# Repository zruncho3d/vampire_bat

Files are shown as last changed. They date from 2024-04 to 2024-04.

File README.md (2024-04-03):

## Vampire Bat - a pinned extrusionless gantry with pin-in-tube belt clips
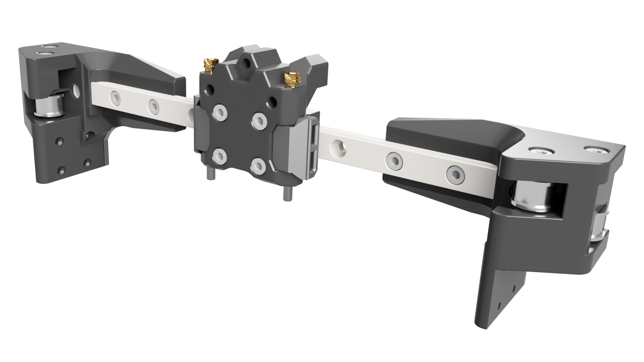
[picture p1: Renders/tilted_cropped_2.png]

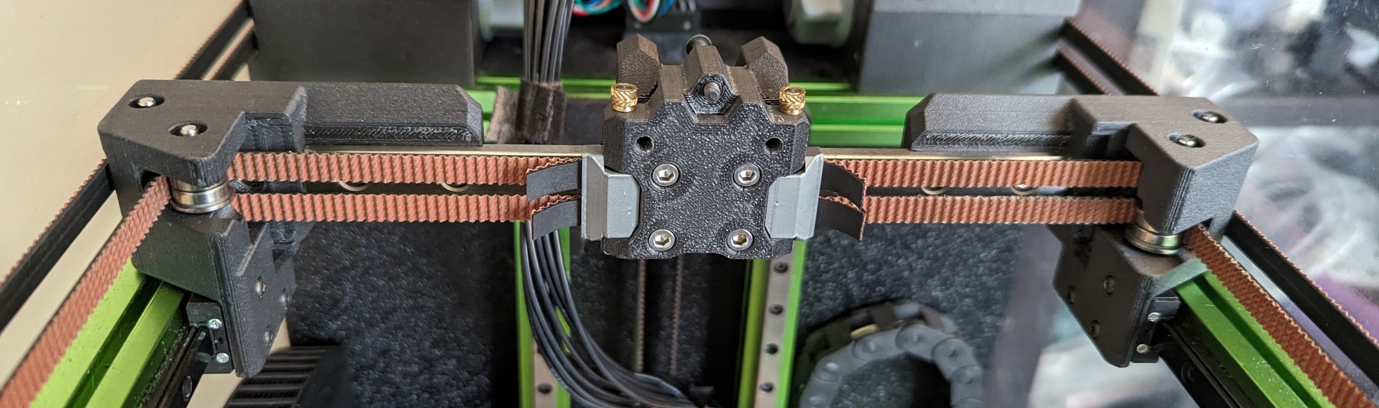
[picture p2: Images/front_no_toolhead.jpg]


The **Vampire Bat** gantry system includes 3 distinct parts:

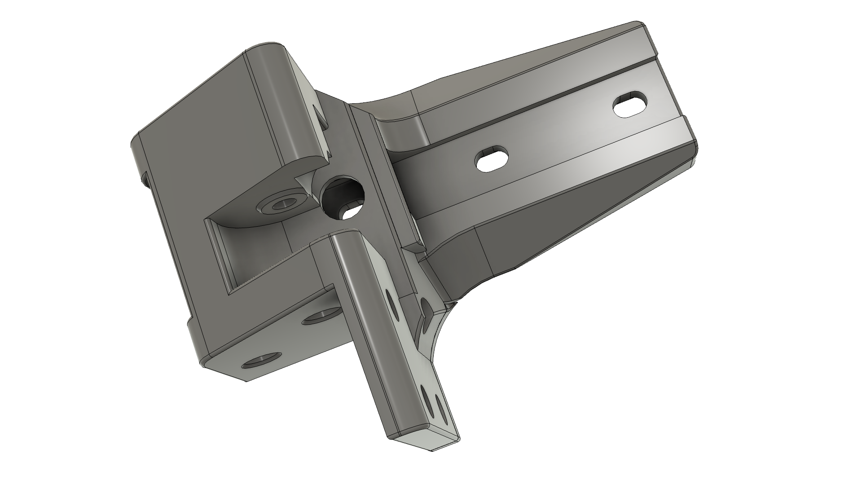
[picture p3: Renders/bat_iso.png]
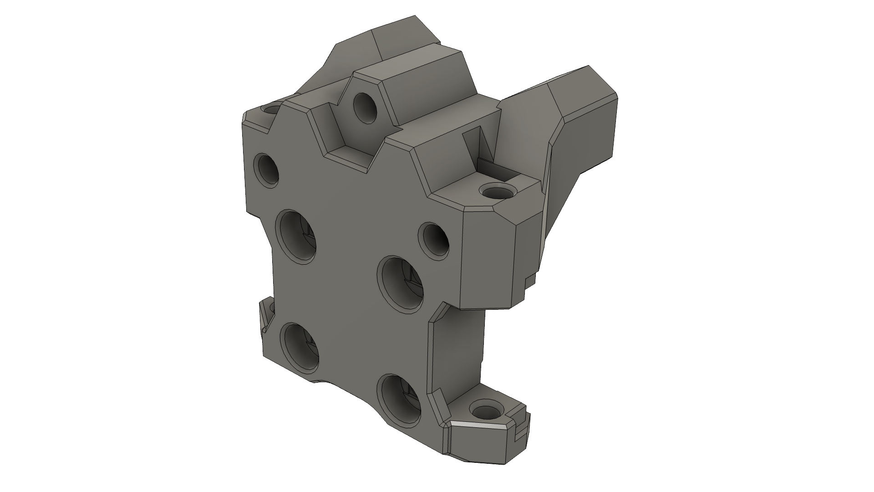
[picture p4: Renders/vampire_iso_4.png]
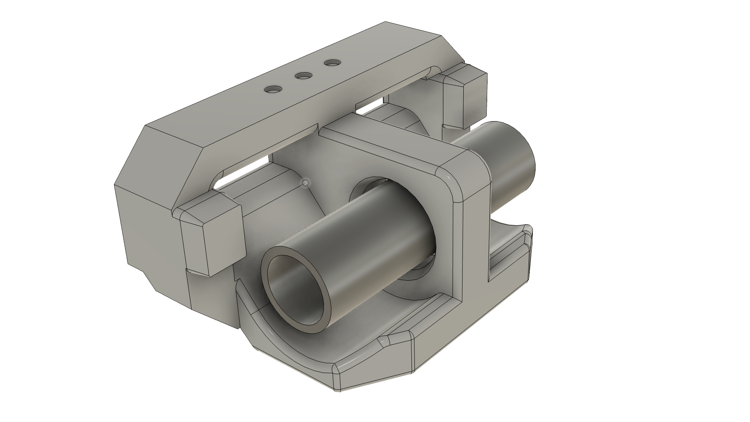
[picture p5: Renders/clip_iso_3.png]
|  |  |  |
| --- | --- | --- |
| **Bat** XY joints | **Vampire** pinned X carriage | **Vampire** pin-in-tube belt clips |

**Together**: these 3 parts yield a rigid, easier-to-build, easier-to-install-belts gantry that drops into an otherwise-stock V0, with little-to-no X or Y travel loss!

**Bat XY joints only**: *Not ready to enter the world of pins, clips, and tubes?  No problem.*    Pick your favorite front-facing X carriage from many choices - Micron, Salad Fork, Pandora/Pandora's Box, Boop, and mmaybe even Archetype and Xol carriages in the future.  Few toolheads fit a V0.2 mount, so more options for interesting new toolheads on smaller printers is a Good Thing.

**Vampire X carriage and clips only**: *Don't have a V0?  No problem.*  Enable the ease of pins on any Micron, Salad Fork, Dueling Zero, or Pandora's Box: faster attachment and completely repeatable tensioning. You can then swap out motors, or swap out rails, in just minutes, without needing to retighten and rematch belt tensions. Should work on any PFA printer with 6mm belts, 3mm belt spacing, and a front-facing MGN9H rail.  

## Updates

* 2024-04-03: Thanks `thor`!  Fixed minor bridging issues near MGN9 entrance and belt tunnel.
* 2024-04-02: Added IS Graphs.

## Features
* Compatibility with MiniSB and derivatives (Mini Stealth Sherpa, Hacky Boi, and more)
* Compatibility with most front-facing PFA carriages, including Boop
* Faster assembly from elimination of both washers and spacers ( :tada: )
* Faster belt installation from more-constrained belt paths; no more poking with an allen key from the side, or needing to remove side panels
* Repeatable belt tensioning; can even remove clips while tensioned
* Supports fully pinned bearings, which prevent over-torqueing that can lead to skipped steps and messy resonance graphs
* All screws are easily accessible when mounted
* Full 120mm+ X and Y travel with BoxZero; ~118mm with regular V0

## Support the creator
Like what you see?  [Buy me a coffee](https://ko-fi.com/zruncho3d) to show the love and enable future mods and content - stuff like [F0](https://github.com/zruncho3d/f-zero), [T0](https://github.com/zruncho3d/tri-zero), [B0](https://github.com/zruncho3d/boxzero), [X0](https://github.com/zruncho3d/double-dragon), [D0](https://github.com/zruncho3d/DuelingZero), [DX](https://github.com/zruncho3d/DuelingX), [ZeroPanels](https://github.com/zruncho3d/ZeroPanels), [ZeroClick](https://github.com/zruncho3d/zeroclick), [NoDropNuts](https://github.com/zruncho3d/f-zero/tree/main/STLs/NoDropNuts), [Poke](https://github.com/zruncho3d/poke), and more.

 :heart: *-Zruncho*

Or, read more below if this seems interesting.....

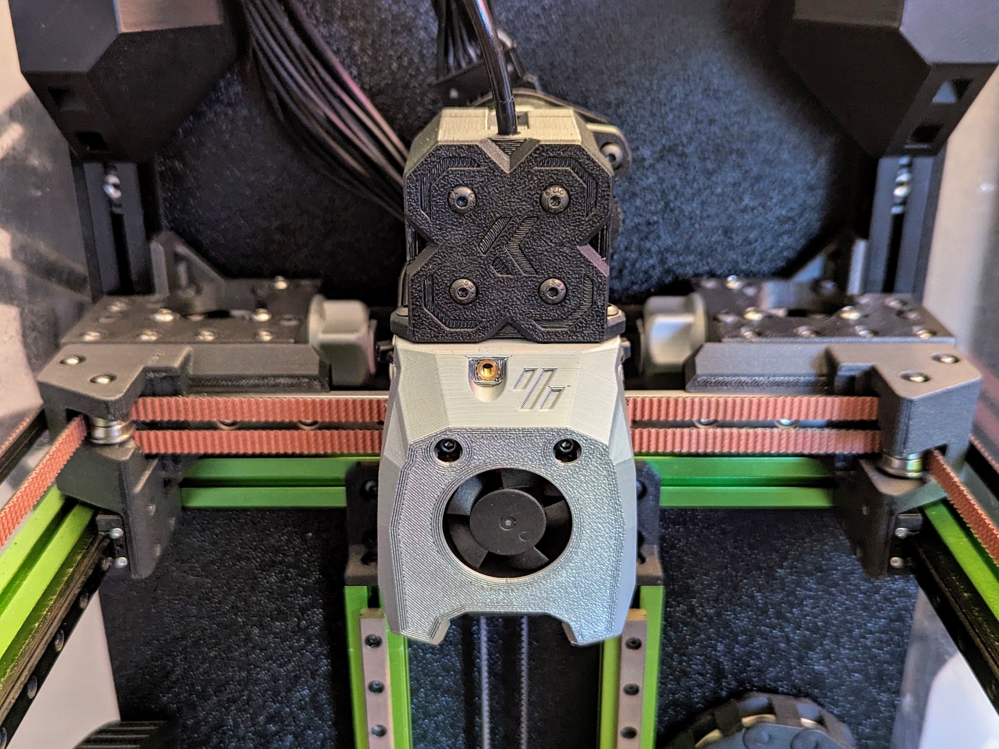
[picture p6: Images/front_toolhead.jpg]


Shown above: gantry parts in 3DXTech CF-ABS + clips in KVP MSIL ABS.  Printer is a custom [Fully-Boxed](https://github.com/zruncho3d/boxzero) [Tri-Zero](https://github.com/zruncho3d/tri-zero) with toolhead by Kevinakasam, plus [Papilio Lite](https://github.com/kevinakasam/Papilio-Belt-Extruder) belt extruder.  This extruder printed the CF-ABS parts like a champ.

## Parts Explained

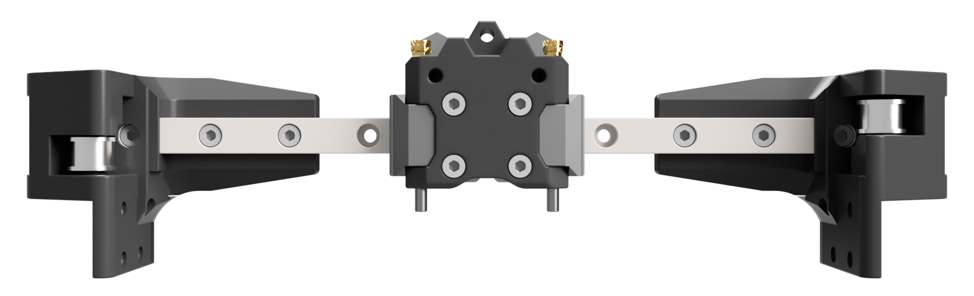
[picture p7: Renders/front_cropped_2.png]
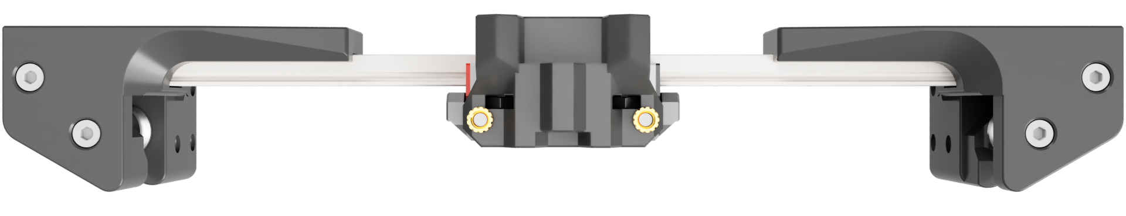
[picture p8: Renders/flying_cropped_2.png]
|  |  |
| - | - |

**Bat XY Joints**: the core idea is to print the XY joints on the rear-facing surface as a single piece, and to constrain the the rail inside (vs as a two-part assembly, on a V0).  Compared to a V0, this is faster and easier to assemble, has way fewer parts (no spacers, washers, or self-tapping screws), is plenty rigid, and is lighter.

The print-orientation concept is based on a [top-facing extrusionless V0 gantry from TheMrFish](
https://discord.com/channels/825469421346226226/875884022285369344/1035022744766652416).  The overall concept is inspired by an [earlier front-facing extrusionless V0 from richardjm](https://github.com/richardjm/voron-parts/tree/main/voron-0.1/Mgn9h).

There's a lot of care to get the tiny vertical bars to acts as supports so that the front-facing filled-in areas can print well.

**Vampire X carriage**: the upper geometry is [Pandora-X-carriage-derived](https://github.com/MasturMynd/Pandora/blob/main/STLs/X_Carriage/MGN9-H_X_Carriage.stl), and includes V0.2-carriage-compatible rear heatset holes for a strain relief or toolhead board.  The CAD derives from [Boop beta-4](https://github.com/PrintersForAnts/Boop/tree/main/beta_4).

**Vampire belt clips**: belts go through a thin slot, then a tube drops in, and the belt wraps around the tube.  The geometry is loosely inspired by [Archetype's clips](https://github.com/Armchair-Heavy-Industries/Archetype/blob/main/Archetype%20Core/Rail%20Mount/%5Ba%5D_belt_clamp_pair.stl), but vastly smaller, and earlier versions were part of [experiments into Pinned Boop](https://www.youtube.com/watch?v=ZaqttrUeE4I).

## Instructions

Required tools:
* (carriage pins option only)
  * small vise
  * ~2.9mm drill bit
* 4mm drill bit for clips
* soldering iron for heatsets

Preferred tools:
* (carriage pins option only) 3mm reamer
* glue

#### Print the parts
* Standard Voron settings are fine.  Add infill beyond 40%, if you'd like; can't hurt.
* This part is near heat; use a temp-resilient material like ABS.

#### Prep the parts
* Remove supports from the XY joints.
* Ream out the two vertical pin holes in the X carriage.  Pins should slide smoothly into the hole.
* Test-fit each tube into a belt clip; may need the 4mm drill bit to open up the hole slightly.
* Test-fit each belt clip into the carriage, and drop the pin in; it should have little to no resistance.  If there's resistance, look through the pin hole and maybe X-acto away a bit of material.
* Screw the 2x M3x30 BHCSes up from the bottom, into the X carriage, until there's a small gap.  Push hard to start forming the threads and make sure they stay aligned against the plastic.
* Assemble pins (2x)
  * Put heatset in a bench vise, with the thin end facing up.
  * Using a 2.9mm or similar drill bit, drill through the hole.
  * Twisting slightly while running the drill, open up the hole on the bottom just a tad, so it tapers.
  * Using the vise, push the pin through the now-slightly-tapered heatset hole, on the wider side; the brass should yield to the steel.  If the heatset breaks, drill a larger hole; 2.95-2.98mm or so is about ideal for a press fit.
* Drop the m3 nuts into the slots on the X carriage; optionally add a small spot of glue, using a toothpick.

#### Assemble the XY joints
* Melt in heatsets (2x) if using screws + heatsets option.
* Push in a bearing pair on an XY joint, then drop in the pin or screw; repeat 4x.
  * Pins may need a little bit of persuasion; align tops of pins to tops of XY joints.

#### Assemble the Gantry
* Push the MGN9 rail in one end, then the other.  Yes, it'll be tight.  Go slow until the screw-holes show the full counterbores.  Be careful.  It will need a fair amount of persuasion, intentionally.
* Align the rail holes to the XY joint holes.
* Add the 6x M3x8 SHCS into the rail holes, then add matching nuts in back. *Don't tighten fully yet*.  The XYs should slide along with the rail.

#### Assemble the X Carriage
* Push the X carriage onto the metal rail carriage, until it clicks and locks. Align it.
* Tighten the 4 M3x8 SHCS for the carriage, fully.
* Tighten the two M3x30 BHCS up from the bottom, fully.

#### Install the gantry and belts
These steps assume no gantry is  present.
* Twist the gantry a bit along the Z axis, and add the two belts from the ABs, pushing through.
* Push two belts from the front idlers through; the channels and bearings should guide the belts through.
* Rotate so the gantry is in the expected position, then set it on the Y carriages.
* Tighten all 8 M2 screws.
* Push or pull on the XY joints until there's no binding during motion; move to test.
* Tigten 6 rail screws, fully.
* Attach first belt clip.
  * Push first belt through, then wrap around, and using pliers to squish the belt against itself, push through the slot, carefully and slowly.  Add tube and tighten until just grabbed.
  * Push second belt through, similarly, and try to match the first in length.  If not the exact same length, keep holding the position, slide it out, and then move it a tooth or two at a time.  Re-push it through and compare.  You want perfect alignment on the first end, to be able to match on the second.
  * Put clip into X carriage and drop the pin in.
* Attach second belt clip.
  * Same as first... but you'll need to put it at a setting that makes it hard, but possible, to put into the "pin position" on the carriage.  You want it to start with a bit of force, as the V0 doesn't have that much tensioner travel.  
  * Once one side feels about right, match the other.  
  * Then, squeezing the clip in, push the pin through.

To release tension, just push up the pin and remove; this is why the spec pin length enables a bit of "overbite", to give more grip.  If still not enough grip, use pliers.  To re-add tension, squeeze again and push the pin through.  Much easier and faster than without pins!  You get faster at putting the clips on, too.

## BOM

Bat XY joints (for set of 2):
* Parts shared with V0 XY joints
  * 8x M2x6 FHCS
  * 6x M3 nuts
  * 8x F623 bearings
* New parts to buy
  * 200mm MGN9H rail: high-preload (Z1)
    * Rails can be slightly shorter (up to 50mm) and may work fine, by using the innermost two screws, instead of 3.
  * 6x M3x8 SHCS
  * Pins Option
    * 4x 3mmx30mm Steel pins
    * 4x M3x4mm "Voron standard" heatsets
  * Screws + Heatsets Option
    * 4x M3x30 SHCS
    * 4x M3x4mm "Voron standard" heatsets

Vampire X Carriage:
* 2x M3x40 BHCS/SHCS (to attach toolhead)
* 2x M3 nut (to attach toolhead)
* 2x 3mmx40mm Steel pins preferred
  * If you can't find these, 35mm, 45mm, and 50mm lengths will work
  * M3x35mm/40mm BHCS/SHCS/FHCS will also work.  
* 2x M3x4mm "Voron standard" heatsets (for rear V0.2 strain relief/toolhead holes)
* 4x M3x8 SHCS (for carriage mounting)
* 1x M3 BHCS/SHCS for (third V0.2 screw) - typically 16mm, but depends on toolhead
* 2x M3x30 BHCS (for carriage stiffening) or SHCS in a pinch

Belt clips (for set of 2):
* 2x tubes: 15mm-long 4mm OD, 3.2mm ID - in Al, Brass, or Steel
  * Slightly shorter, like 14.8mm, may help with insertion.  File to length.

### Status: Experimental

Until there are a bunch of builds, it'll be categorized as beta/experimental, but...

Zruncho has been using a weaker extrusionless gantry and pinned carriage (from Pinned Boop) for all of 2023 without ill effects.

### Resonance testing

Graphs are from a Boxed Tri-Zero with experimental dropped Z extrusions, PapLite, Kevinakasam MiniSB-derived toolhead, GT2 belts, Vampire Bat gantry, and Mellow ADXL345 with CNC mount.

Roughly 30K is pretty good.  

Note the low spectral density on X (200) vs Y (9000); a high preload rail may be causing low-frequency attenuation effects here.  This should be a fast swap to test, though... no need to retension belts!

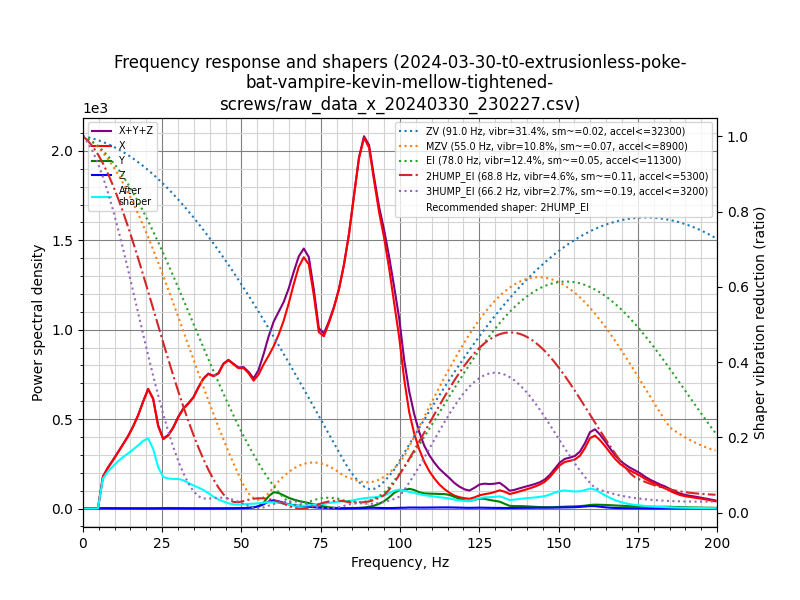
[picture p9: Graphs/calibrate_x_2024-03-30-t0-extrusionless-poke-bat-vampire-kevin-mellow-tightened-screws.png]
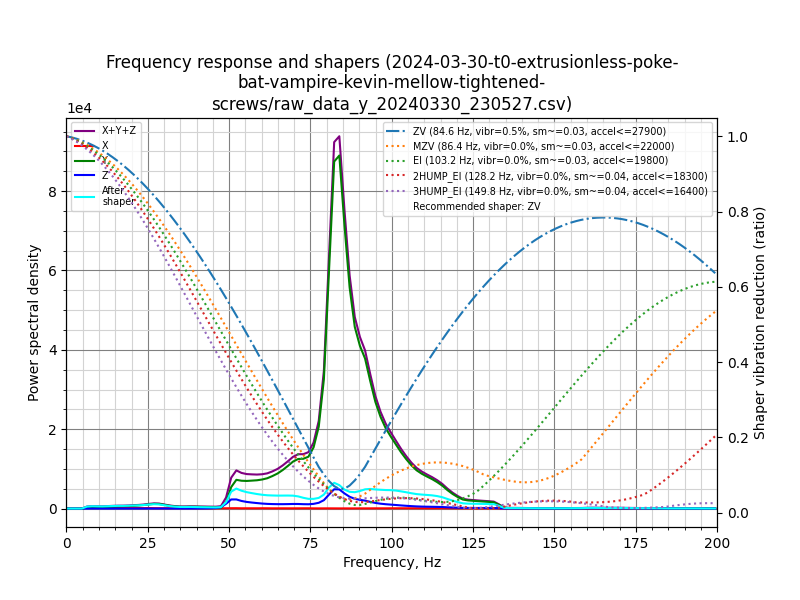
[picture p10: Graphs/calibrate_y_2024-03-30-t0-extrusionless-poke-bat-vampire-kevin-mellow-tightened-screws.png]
|  |  |
| - | - |
| X: 32K | Y: 28K |

### CAD Note: flip the parts after STL export!

The CAD shows the wrong chirality - that is, the filled-in areas were done in a way that doesn't match the V0 convention, so it will NOT work if you just print the parts from CAD.  It's too much CAD work to flip the chirality, so the parts are all mirrored after STL export.  MAKE SURE to mirror if you use the CAD and do any exports.  

Note, all STLs here are pre-mirrored to the correct orientation, so if you just grab the STLs, *you don't need to do anything*.

### FAQ

#### Why the name?

The pins stick out a bit, creating an overbite, making the Vampire carriage the first part here to be named.

When combined with an MGN9 rail, the XY joints kind look like a bat from the front and top.

It even kinda looks like a vampire bat!  The carriage has eyes, ears, a mouth, and teeth.

Did you know? Vampire bats are the only mammals to have evolved to feed exclusively on blood, a trait called hematophagy (according to [Wikipedia](https://en.wikipedia.org/wiki/Vampire_bat)).  

#### Is going extrusionless a bad idea?

Think about it: on something as small as the V0, the toolhead and frame are more likely to be the limiter than the gantry not having a backing extrusion.  This is not how machine tools are supposed to be designed; the extrusion or backer helps lock the rail flat, and in place.  

But in practice, it all seems just fine, and the options that having a front-facing rail opens up - those seem worth it.  The lack of a flexible plastic L shape might help with resonances, as does the removal of 25-30g from the extrusion.

More importantly, in practice, it prints fine, and the IS results are fine.  Other stuff seems to matter more: rail quality, toolhead design/weight, and frame rigidity.

## Future work
If this gets traction...
* More sizes - the f3d file is parametric, and scales to different numbers of backing nuts, with varying overhang and Y-carriage holes shifts... but it became fragile right before release, so this isn't an advertised feature.
* "Perimeter adders" - tiny slots, to add material without needing to change settings, like Boop has.
* Sanding tool - would be helpful to get the tubes the right length, without getting an unwanted angle.

### Special Credits:
* **Thor** for helping talk through various design concepts.
* **Leddhedd** for helping think through various clip options.

### Timeline
* 2024-03-31: April Fool's Eve release! :tada:
* 2024-03-30: Resonance tests show nothing of interest :thumbsup:
* 2024-03-24: Nuts moved behind pins, to enable 8-9mm thickness
* 2024-03-14: Vampire carriage takes shape at thicker 12mm depth
* 2024-03-14: Spacers and washers eliminated
* 2024-03-10: Bat gantry first modeling and first prints
* 2023-midyear: Belt clip testing with Pinned Boop

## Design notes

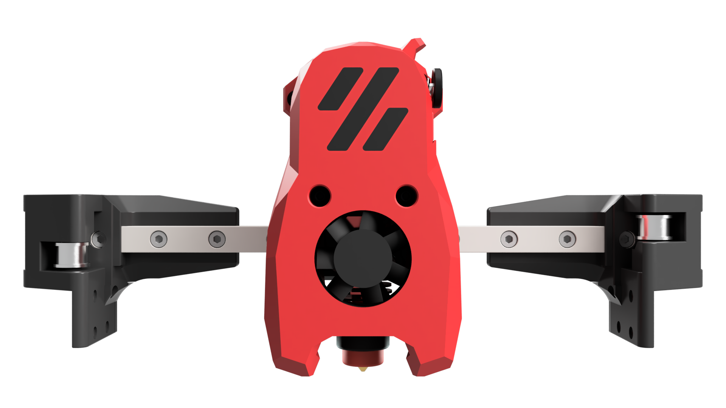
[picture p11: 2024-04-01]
Renders/toolhead_front.png

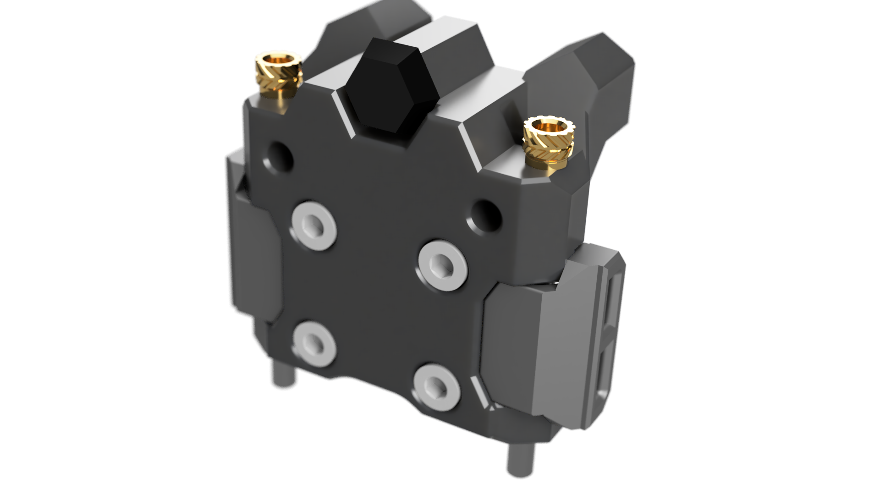
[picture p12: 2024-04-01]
Renders/vampire_iso.png

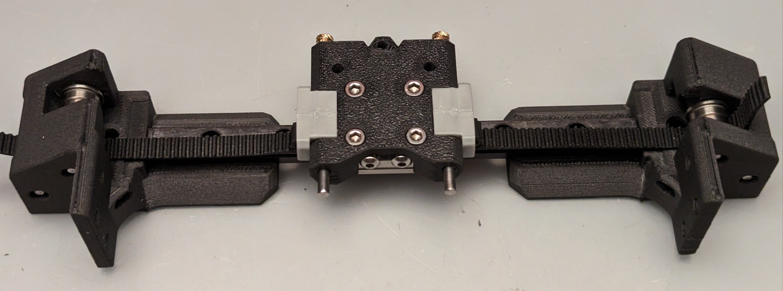
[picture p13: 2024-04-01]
Images/top_shifted.png

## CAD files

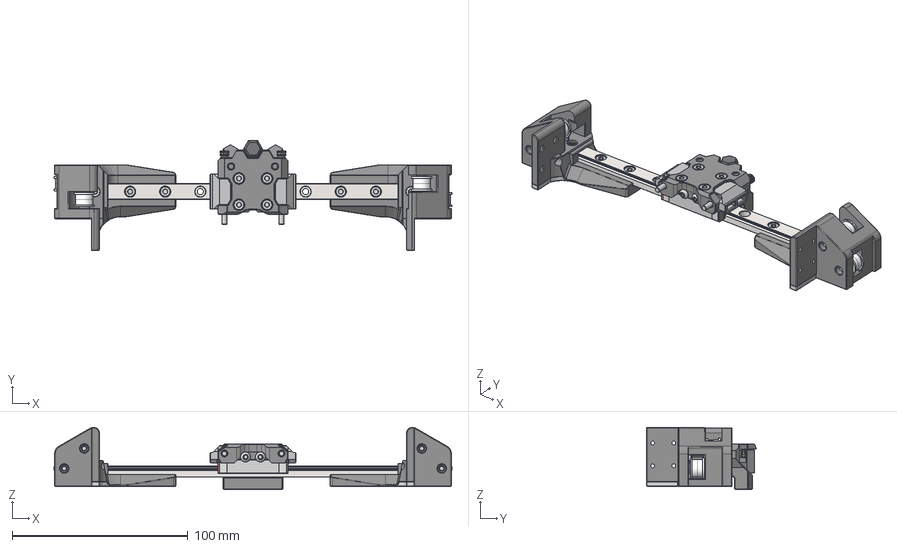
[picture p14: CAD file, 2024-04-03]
CAD/Bat_Gantry_v24.step
226.7 x 62.6 x 35.3 mm
XY Joint Left
XY Joint Right
MGN9 200mm - Linear Rail
MGN9H - Carriage
MGN9H - Carriage (1)
MGN9H - Carriage (2)
MGN9H - Carriage (3)
MGN9H - Carriage (4)
MGN9H - Carriage (5)
MGN9H - Carriage (6)
MGN9H - Carriage (7)
MGN9H - Carriage (8)
M3x8 SHCS v1 x 6
M3x25 SHCS x 4
F623-RS (2) (1) x 8
support
M3 Threaded Insert v3 (3) x 2
Clip x 2
Tube x 2
M3x8 SHCS v1_1 x 4
M3x30 BHCS v1 x 2
M3_Hexnut x 2
XY Joint Left (1) (1)
XY Joint Left (1)
XY Joint Right (1) (1)
XY Joint Right (1)

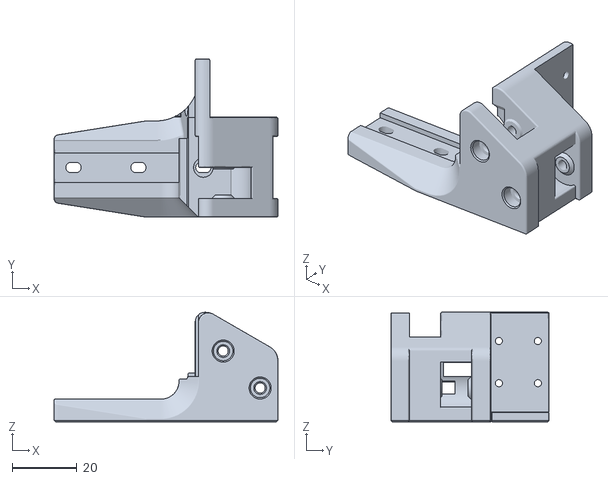
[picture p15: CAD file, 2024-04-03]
STLs/Bat_XY_Left.stl
69.0 x 48.8 x 33.7

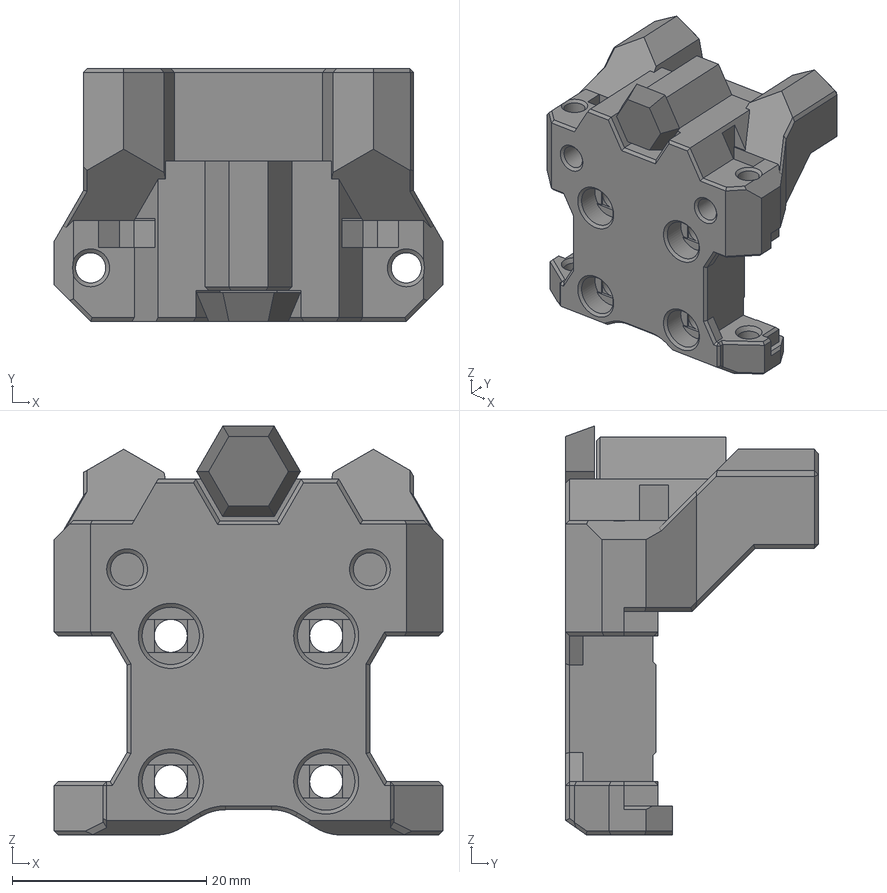
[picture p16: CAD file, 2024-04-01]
CAD/Vampire_X_Carriage_v38.step
40.0 x 26.0 x 42.1 mm

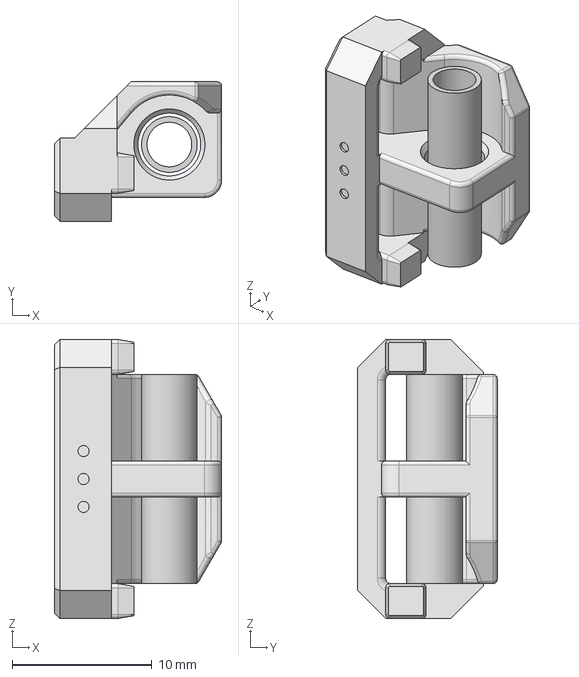
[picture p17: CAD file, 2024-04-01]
CAD/Vampire_Clip_v9.step
12.0 x 10.0 x 20.0 mm
Clip
Tube

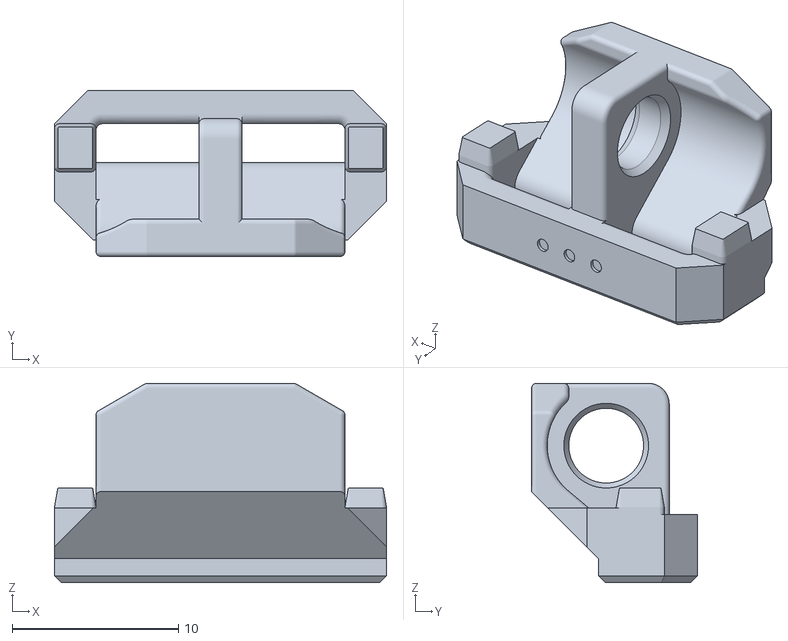
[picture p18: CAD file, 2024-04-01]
STLs/Vampire_Clip_2x.stl
20.0 x 10.0 x 12.0

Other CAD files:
STLs/Bat_XY_Right.stl
CAD/Vampire_Clip_v9.f3d

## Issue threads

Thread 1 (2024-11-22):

Add 3mm to toolhead_screw_depth

noobydp, 2024-11-22:
I'm using the dragon burner spacer with the vampire carriage which means I need to use longer bolts to attach the DB toolhead+spacer as the 40mm bolts arent long enough.

With the current toolhead_screw_depth of 12.4, there isnt enough clearance for a 50mm bolt, but increasing it by 3mm to 15.4 should be enough.

I havent reprinted the carriage yet but I couldnt see this change breaking anything else.

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

Micah-Scheck, 2025-03-02:
Hi, do you have a link to the Delta Burner spacer? I cant seem to find it anywhere

noobydp, 2025-03-04:
Hey, here's the one I was using.

[Spacer.zip](https://github.com/user-attachments/files/19065782/Spacer.zip)

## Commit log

2024-04-01 First public release
    [Bat_Gantry_v20.step, Bat_XY_Left.stl, Bat_XY_Right.stl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]
2024-04-03 Fix bridging issues - thanks Thor
    [Bat_Gantry_v20.step, Bat_Gantry_v24.step, Bat_XY_Left.stl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]
